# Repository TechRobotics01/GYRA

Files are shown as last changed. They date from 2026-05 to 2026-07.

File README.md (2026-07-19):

# GYRA 
So "GYRA" is a 3-axis stabilization gimbal system i built for phones and lighteight cameras more specifically point and shoot cameras<br>
GYRA is fully custom built from the 3D Design to the motherboard PCB all made by ME <br>
The name "GYRA" i derived from gyroscope which is a part of the MPU6050 sensor used in this project and GYRA also sounds pretty cool too <br>

# PURPOSE
So why exatly does this project exist <br>
This project exists because of a few reasons
- cheaper solution to ronin gymbals 
- extremely good learning project 
- fully custom built so i can easily add my own features

# FEATURES
- based on ESP32 S3 WROOM-1
- Fully custom 3D designed parts
- MPU6050 and HMC5883L used for motion tracking
- Portable design
- Custom PCB
- Designed for phones / lightweight cameras (upto ~ 200g)

# HOW DOES IT WORK
The mpu6050 and HMC5883L countinuously track the relative motion of the gimbal and then send the signals to the motherboard the ESP32 based motherboard then processes the signals to understand the orientation and run 3 seperate PID loops for 3 seperate axes namely 
- YAW
- ROLL
- PITCH
After the signals are passed through an Alpha filter for clearning the NOISE then are send to their respective PID loop the values i found which work for this system are
- For roll and Pitch axis
- Kp->1.2
- Ki->0
- Kd->0.1

I havent't really found the perfect values for the yaw axis as the yaw axis is the most unstable axis of the 3 axes and needs propery callibration  even more precise PID tuning for proper axis stability 

These 3 PID loops are the heart of the program these loops need to be very precise for proper theoretical working of the system <br>
I have a very good reason why i am using the word Theoretical
because in reality the project suffered from bracket instability joint wobble and print arm fles during the prototype phase which i worked hard to eliminate in MARK-1

# HARDWARE
## 3D PRINTABLE ASSEMBLY 
here is a render of the 3D printable design 
GYRA marl-1 with camera
GYRA EXPLODED PNG
The entire assembly consists of a total of 6 files which are 
- HEXALEGGED BASE (PCB housing)
- PCB HOUSING LID
- BASE HANDEL
- YAW ARM
- YAW--ROLL ARM
- ROLL--PITCH ARM
All of these are connected by mostly standard M3 screws whereas M2 screws may be required at some places such as the last 2 screws at ever arm of the 25T Aluminium CNC servo spline

## PCB / elecronics 
The pcb consists of the following majour parts 
- ESP32 S3 WROOM-1 module
- JST Connectors for
  - MPU6050 (4-pinJST)
  - HMC5883L (4-pinJST)
  - SERVOS(incuding GND) (4-pinJST)
  - Battery connector (2Pin JST)
- Decoupling capacitors
- IO0 and EN switched (SMD)
- M3 mounting hole




Now here comes the important part for the connnections so no-1 you need to first of all connect the 6-li-ion battries enclosed in the base handle to a 2S BMS module and to a DC femlae jack for charging and then you need to diectly connect the VCCs and GNDs of the servos to the BMS module and now you need to make a 4 pin JST connector which is basically 3 pins for servos yaw-roll-pitch respectively and final pin GND.

Now after this you need to  take the battry 7.4V and then connect it directly to the PCB as the PCB has a internal Step-Down voltage circuit but you need to be careful with the polarity. 

Please refer to the PCB schematics while hotplate soldering / assembling your PCB because the BARE PCB does not have much marking as to such where which pin should be conected 

# ZINE PAGE 
GYRA

# BUILT IRL 
Demo Video- https://youtu.be/y3TJgLPC-Hc





GYRA has been built IRL!

# HOW TO BUILD IT FOR YOURSELF 
So you want to make this project for yourself too <br>
I have included each and every file and component that you will require in this repository and BOM 
STEP-1
- Buy all the parts in the BOM
- Print the parts inside the Mark-1--->>STEP FILE folder (total of 6 parts)
- Get the PCB fabricated and solder all the components neatly using the HOTPLATE
- Test the PCB for any imporperly soldered parts/components
- Assemble the pcb inside the 3D printed hexalegged base using M2 screws
- Now connect the battries in a 2S3P manner
- Cut and strip the wires and make it into a JST connector
  - 1 FOR MPU6050
  - 1 FOR HMC5883L
  - 1 FOR SERVOS AND GND PIN
  - 1 FOR THE BATTERY connector
  - Solder the battery connections as stated under the "PCB / electronics part" and then house the battires inside the base handle
  - Join the hexalegged base to the pcb lid using M3 and M2 screws whereever needed
  - now assemble the above appembly consisting of
    - Servos
    - IMUs
    - YAW arm
    - YAW---PITCH arm
    - PITCH----ROLL arm
    - And then finally connect the 1/4th inch thread to the print
    - Connect your camera or phone adapter
    - Finally please use the code to TUNE your gimbal different tuning values are needed for different cameras because center of mass and orientation
    - Affect the PID constants a lot
    - After tuning your gimbal please hardcode the values into the gimbal (more info on that in a few days)
    - And finally enjoy a gimbal you made!!!!  
    WARNING: you may need to heat the 1/4th inch screw to 100*C so it can be properly housed inside the PITCH arm

# PROBLEMS FACED
there were a lot of problems i faced during the development of this project i have all the prototypes saved in subfolders in the CAD filder this project had a total of 5 iterated prototypes before i made the actual MARK-1 <br>
so here is a list of probelms i faced <br>

So first of all i had no inspiration and was designing the structure i had in my head when i built and tested the first printed prototype i found out many many fatal flaws such as the biggest one being that the roll arm was colliding with the base of the YAW arm where the sensor was seated and also that the motor constrians were misjudged second of all the arms were flexing because i made then longer than they needed to be and the arm used to jitter and shake because the motor could not take the load of the heavy arms and assembly <br>

after like 3 iterations i finally took a bit of inspiration from ronin's gimbal and finally understood how the gimabl's standard structure should actually be first of all i was veru skeptical about if the motors could move the long arms or not as the length of the arms were almost excedding  the torue the motors could produced but once it was assembeled nd i tested it....IT worked just fine <br>

Now here comes the biggest challenge i faced almost throughtout the project so first of alli was using MG995 motors's plastic head and attachments to connect the 3D printed arm with the motor which was an bad idea because it already had a bit of play which was only made worse by the motor repeatedly moving and wearking out the joint's teeth during Prottype's PID tuning and i found out the solution to this when i was sitting in my room at 12 AM and the idea of using CNC Aluminium 25T servo spline arm <br>

 This thing and now i designed the nre joint in accordance to the dimension's of the spline and i used properl M3 and M2 screws to mount the print on this isntead of using improper sized M2.2 screws everywhere and hoping it would work 

 Overall this project was one of the best learning project i had made because it taught me many things related to 3D printing CAD and print tolerances
 and also sharpened my skills of PCB and Embedded design design and overall project design and workflow 
 The multiple failed prototypes challenged the appumptions i made and i developed a new kind of more efficient workflow than before 
 
### I SPENT A TOTAL OF ~68 HOURS ON THIS PROJECT ###

# CREDITS 
- ME
- google.com
- chatgpt (FOR DEBUGGING AND GUIDANCE ONLY)
- [randomnerdtutorial.com](https://randomnerdtutorials.com/)

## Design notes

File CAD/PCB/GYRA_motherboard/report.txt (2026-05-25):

Plotted to 'C:\Users\DELL\Desktop\MISSION FALLOUT\GYRA\GYRA\CAD\PCB\GYRA_motherboard\GYRA_motherboard-F_Cu.gbr'.
Plotted to 'C:\Users\DELL\Desktop\MISSION FALLOUT\GYRA\GYRA\CAD\PCB\GYRA_motherboard\GYRA_motherboard-B_Cu.gbr'.
Plotted to 'C:\Users\DELL\Desktop\MISSION FALLOUT\GYRA\GYRA\CAD\PCB\GYRA_motherboard\GYRA_motherboard-F_Paste.gbr'.
Plotted to 'C:\Users\DELL\Desktop\MISSION FALLOUT\GYRA\GYRA\CAD\PCB\GYRA_motherboard\GYRA_motherboard-B_Paste.gbr'.
Plotted to 'C:\Users\DELL\Desktop\MISSION FALLOUT\GYRA\GYRA\CAD\PCB\GYRA_motherboard\GYRA_motherboard-F_Silkscreen.gbr'.
Plotted to 'C:\Users\DELL\Desktop\MISSION FALLOUT\GYRA\GYRA\CAD\PCB\GYRA_motherboard\GYRA_motherboard-B_Silkscreen.gbr'.
Plotted to 'C:\Users\DELL\Desktop\MISSION FALLOUT\GYRA\GYRA\CAD\PCB\GYRA_motherboard\GYRA_motherboard-F_Mask.gbr'.
Plotted to 'C:\Users\DELL\Desktop\MISSION FALLOUT\GYRA\GYRA\CAD\PCB\GYRA_motherboard\GYRA_motherboard-B_Mask.gbr'.
Plotted to 'C:\Users\DELL\Desktop\MISSION FALLOUT\GYRA\GYRA\CAD\PCB\GYRA_motherboard\GYRA_motherboard-Edge_Cuts.gbr'.
Created Gerber job file 'C:\Users\DELL\Desktop\MISSION FALLOUT\GYRA\GYRA\CAD\PCB\GYRA_motherboard\GYRA_motherboard-job.gbrjob'.
Info: Done.
Info: Done.

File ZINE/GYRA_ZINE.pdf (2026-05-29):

# GYRA

## A Fully Custom Built 3-Axis Gimbal

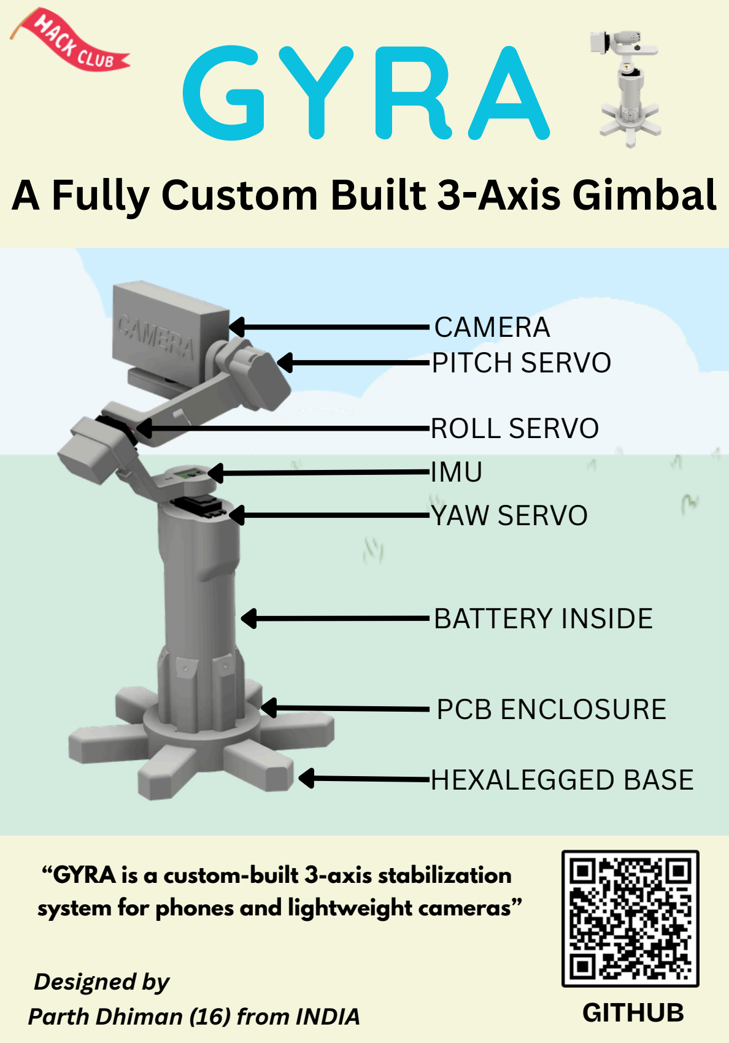
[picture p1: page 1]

HEXALEGGED BASE

BATTERY INSIDE

PCB ENCLOSURE

IMU

PITCH SERVO

“GYRA is a custom-built 3-axis stabilization system for phones and lightweight cameras”

YAW SERVO

ROLL SERVO

Parth Dhiman (16) from INDIA

GITHUB

CAMERA

Designed by

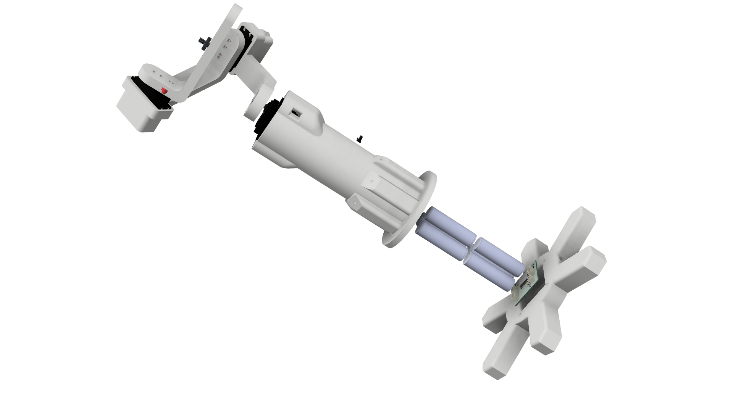
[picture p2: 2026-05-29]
RENDERS/MARK-1 RENDERS/GYRA EXPLODED PNG.png

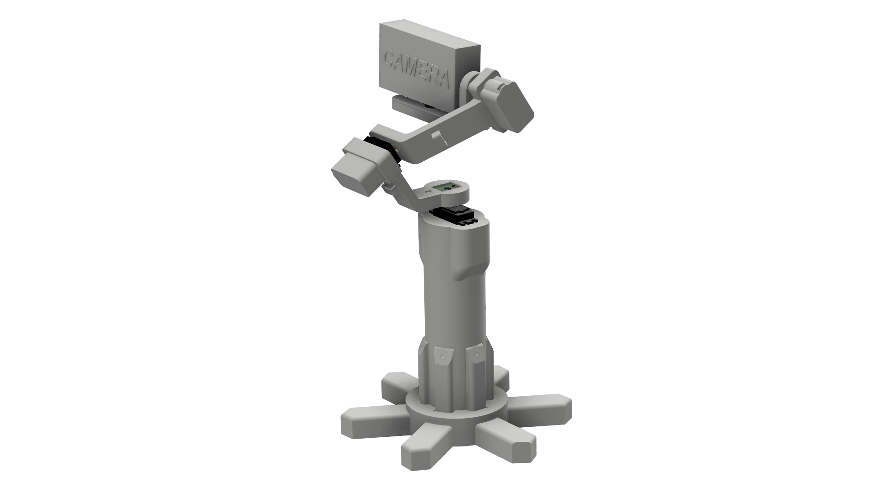
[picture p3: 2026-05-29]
RENDERS/MARK-1 RENDERS/GYRA marl-1 with camera.png

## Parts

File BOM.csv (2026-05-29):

S. No | Part Name | Qty required | Qty Purchased | Cost per Unit($) | Shipping cost ($) | Total cost ($) | Status | Supplier | Purchase Link
1 | 1kg PLA+(eSun) | 1 | 1 | 11.49 | NA | 11.49 | Needed | robocraze | https://robocraze.com/products/esun-pla-basic-1-75mm-1kg-3d-printing-filament-black-color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
2 | MPU6050 | 1 | 1 | NA | NA | NA | Already owned | NA | NA
3 | HMC5883L | 1 | 1 | 1.98 | NA | 1.98 | Needed | robocraze | https://robocraze.com/products/hmc5883l-triple-axis-compass?variant=40192560857241
4 | MG995 servos | 3 | NA | NA | NA | NA | Already owned | NA | NA
5 | 18650 Li-ion battries | 6 | 6 | 0.72 | NA | 4.32 | Needed | robocraze | https://robocraze.com/products/3-7v-2000mah-18650-li-ion-battery?_pos=1&_sid=db8a20379&_ss=r
6 | 2S Li-Ion BMS | 1 | 1 | 0.37 | NA | 0.37 | Needed | makerbaxxar | https://makerbazar.in/products/18650-bms-lithium-battery-protection-board?variant=48251032731888
7 | DC power jack(male) | 1 | 1 | 0.089 | NA | 0.089 | Needed | makerbazzar | https://makerbazar.in/products/5-5-2-1mm-dc-power-jack-wire-with-open-end?variant=47599032140016
8 | DC power jack(female) | 1 | 1 | 0.094 | NA | 0.094 | Needed | maker bazzar | https://makerbazar.in/products/5-5-2-1mm-dc-power-jack-wire-with-open-end?variant=47599032172784
9 | PCB Fab. | 1 | 5 | 8.36 | 1.51 | 9.87 | Needed | LionCircuits | https://order.lioncircuits.com/cart
10 | M3 screws | 15 | NA | NA | NA | NA | Already owned | NA | NA
11 | M2 screws | 10 | 25 | 0.082 | 1.46 | 3.51 | Needed | Onlyscrews | https://onlyscrews.in/products/m2-x-10mm-hex-allen-socket-head-high-tensile12-9-black-oxide-screw-dia-2mm-length-10mm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
12 | 4pinJST Connector (female) | 4 | 4 | 0.17 | NA | 0.68 | Needed | Robu | https://robu.in/product/1-0c-04y-1mm-4-pin-ultra-thin-female-housing-connector-with-300mm-wire28-awg/
13 | 4pinJSt connector(male) | 4 | 4 | 0.048 | NA | 0.192 | Needed | Robu | https://robu.in/product/a2512wv-4p-cjt-4-pin-2-50mm-180-wafer-male-connector-rohs/
14 | 4.7uH inductor | 1 | 5 | 0.25 | NA | 1.25 | Needed | Robu | https://robu.in/product/cd43-4-7%C2%B5h-1a-smd-power-inductor-5-pcs/
15 | DIODES AP63203WU-7 | 1 | 2 | 0.9 | 1.05 | 2.86 | Needed | LionCircuits | https://www.lioncircuits.com/parts/AP63203WU-7
16 | ESP32 S3 WROOM-1 | 1 | 1 | 4.5 | 0.89 | 5.39 | Needed | Techeism | https://techiesms.com/product/esp32-s3-wroom-n16r8/
17 | Servo spline arm 25T | 3 | 3 | 0.68 | NA | 2.04 | Needed | Robu | https://robu.in/product/cnc-aluminum-steering-servo-horn-arm-futaba-standard-25t-aluminum/
18 | soldering station | 1 | 1 | 15 | NA | 15 | Needed | Robu | https://robu.in/product/yihua-926-upgrade-version-soldering-iron-station/
 |  |  |  |  | TOTAL COST | 59.135

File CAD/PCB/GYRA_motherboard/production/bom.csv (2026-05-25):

Designator | Footprint | Quantity | Value | LCSC Part #
C1 | 0805 | 1 | 1uF
C2, C8 | 0805 | 2 | 10uF
C3, C6 | 0805 | 2 | 0.1uF
C4, C5 | 0805 | 2 | 22uF
C7 | 0805 | 1 | 100nF
J1 | JST_XH_B4B-XH-A_1x04_P2.50mm_Vertical | 1 | MPU6050
J2 | JST_XH_B4B-XH-A_1x04_P2.50mm_Vertical | 1 | HMC5883L
J3 | JST_XH_B4B-XH-A_1x04_P2.50mm_Vertical | 1 | SERVOS
J4 | JST_XH_B2B-XH-A_1x02_P2.50mm_Vertical | 1 | 2S3P BAT
L1 | L_7.3x7.3_H4.5 | 1 | 3.9uH
R1, R2 | 0805 | 2 | 10KR
SW1 | SW_Push_1P1T_NO_CK_KMR2 | 1 | SW_EN
SW2 | SW_Push_1P1T_NO_CK_KMR2 | 1 | SW_IO0
U1 | ESP32-S3-WROOM-1 | 1 | ESP32-S3-WROOM-1
U2 | TSOT-23-6 | 1 | AP63203

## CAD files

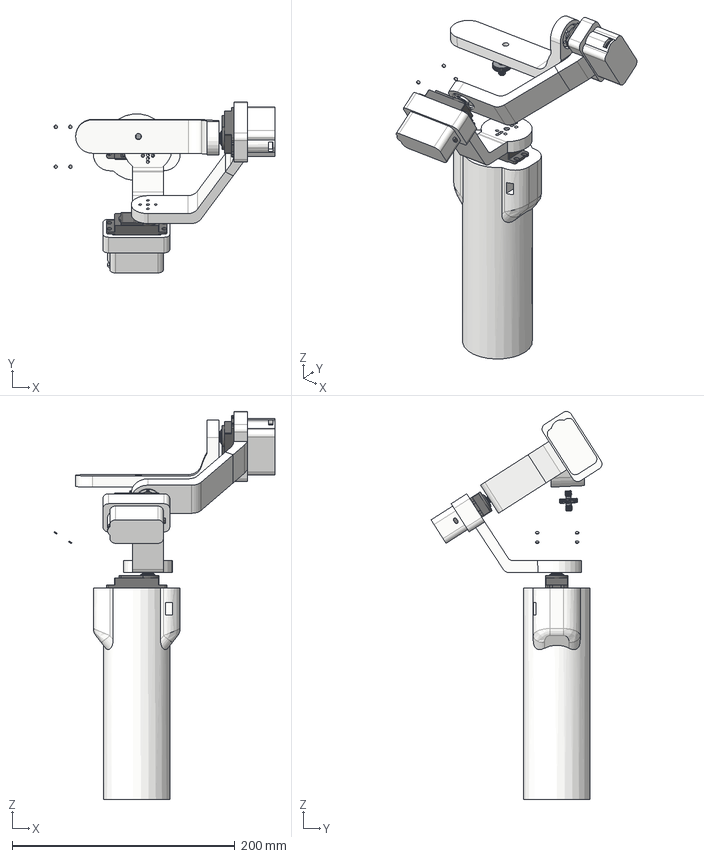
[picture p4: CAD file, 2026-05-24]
CAD/CAD 3D/MARK-1/ASSMEBLY STEP FILE/GYRA MARK-1 ASSEMBLY .step
198.2 x 153.4 x 348.3 mm
MG995_Gear2
Servo horn v2 x 2
GYRA ROLL PITCH BRAKET PROTOTYPE V2
GYRA PITCH BRACKET
ADAPTER_1-4_M_1-4_M.PRT
GYRA PITCH ARM V4
18650 Battery x 6
GYRO base handle axis 1 (yaw)

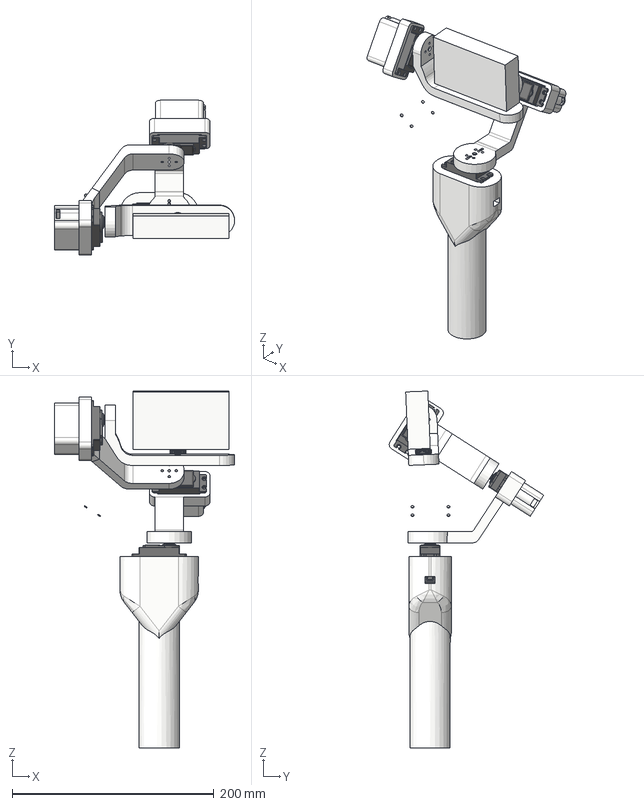
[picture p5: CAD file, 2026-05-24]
CAD/CAD 3D/PROTOTYPES/PROTOTYPE V5/ASSEMBLY/GYRA PROTOTYPE V5 FULL ASSEMBLY v13.step
178.9 x 153.4 x 354.3 mm
GYRO base handle axis 1 (yaw)
MG995_Gear2
Servo horn v2 x 2
GYRA ROLL PITCH BRAKET PROTOTYPE V2
GYRA PITCH BRACKET
ADAPTER_1-4_M_1-4_M.PRT
GYRA PITCH ARM V4

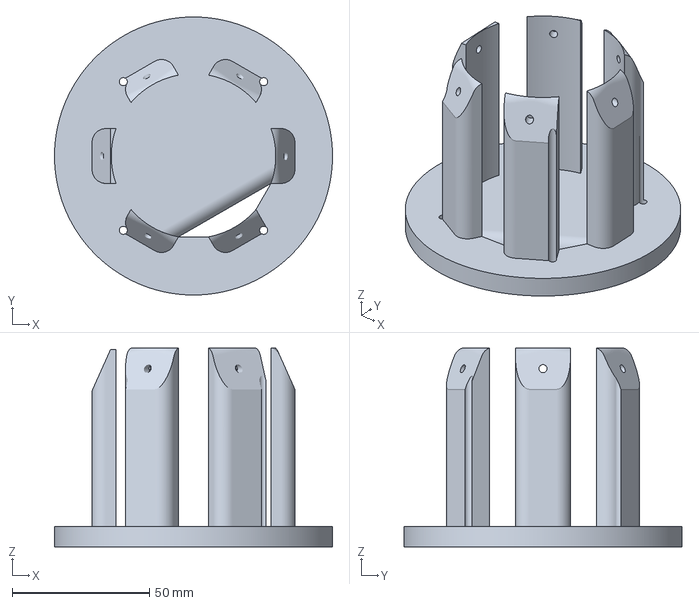
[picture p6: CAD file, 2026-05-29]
CAD/CAD 3D/MARK-1/3D PRINT FILES/BAMBU SLICER/GYRA PCB BASE LID v8.3mf
101.4 x 101.4 x 72.5 mm

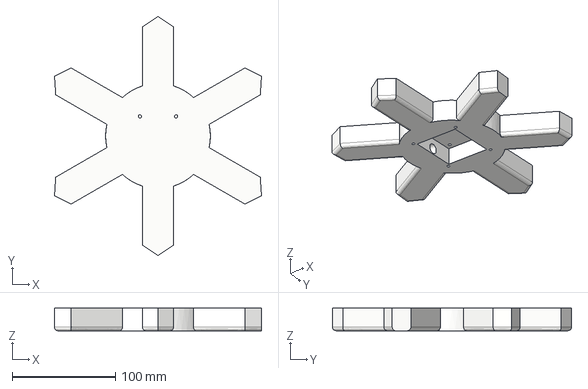
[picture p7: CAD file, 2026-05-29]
CAD/CAD 3D/MARK-1/3D PRINT FILES/STEP FILES/GYRA BASE PCB ENCLOSURE v9.step
200.4 x 231.4 x 22.0 mm

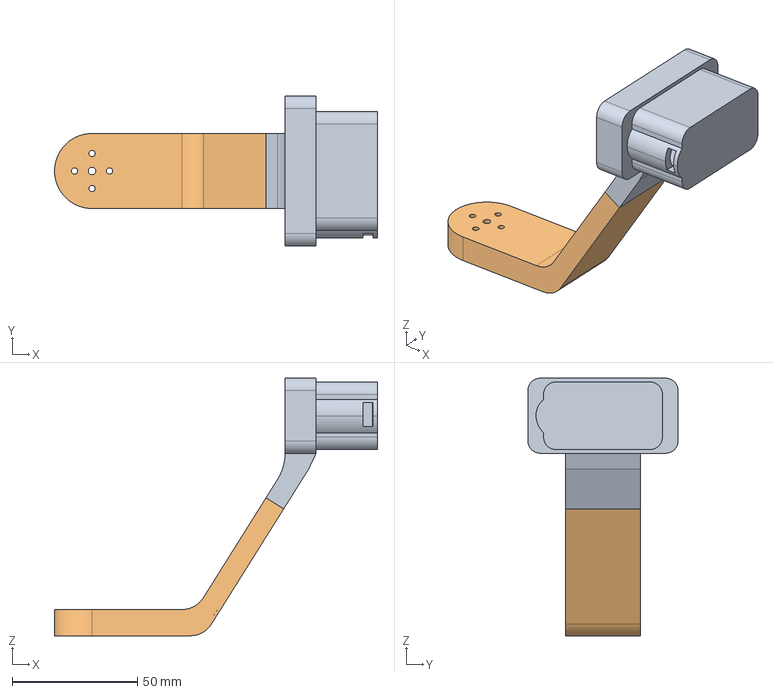
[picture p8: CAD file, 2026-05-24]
CAD/CAD 3D/PROTOTYPES/PROTOTYPE V5/3D PRINTABLES/GYRA PITCH BRACKET v31(PRT 2).step
129.0 x 60.0 x 102.9 mm

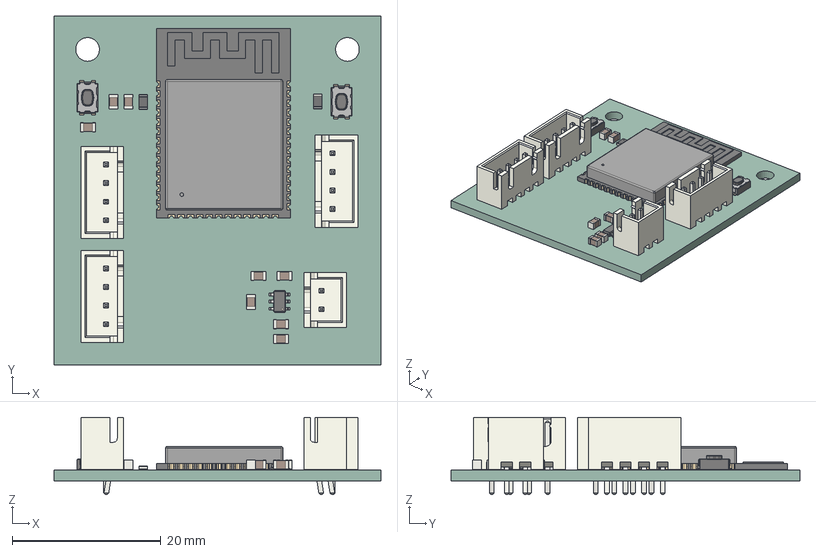
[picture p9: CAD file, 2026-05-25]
CAD/PCB/PCB_STEP_FILE/GYRA_motherboard.step
44.0 x 47.0 x 10.4 mm
SW_Push_1P1T_NO_CK_KMR2 x 2
TSOT-23-6
JST_XH_B4B-XH-A_1x04_P2.50mm_Vertical x 3
C_0805_2012Metric x 8
ESP32-S3-WROOM-1
JST_XH_B2B-XH-A_1x02_P2.50mm_Vertical
R_0805_2012Metric x 2
GYRA_motherboard_PCB

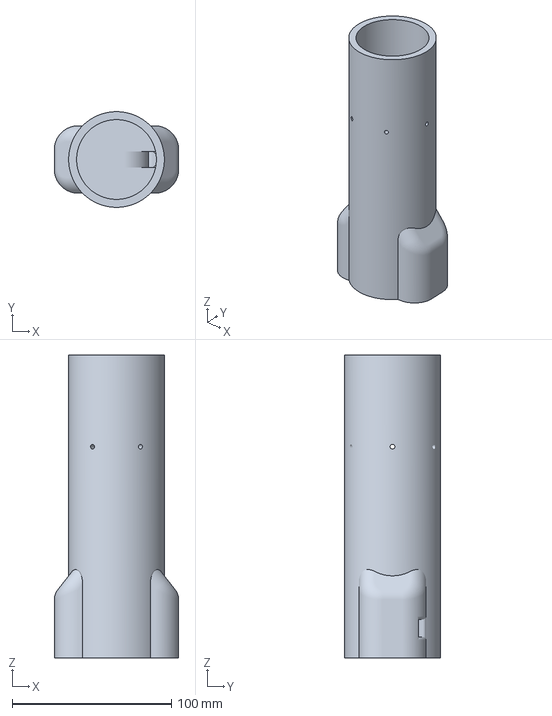
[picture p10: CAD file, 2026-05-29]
CAD/CAD 3D/MARK-1/3D PRINT FILES/BAMBU SLICER/GYRO base handle axis 1 (yaw) v12.3mf
78.0 x 60.0 x 190.0 mm

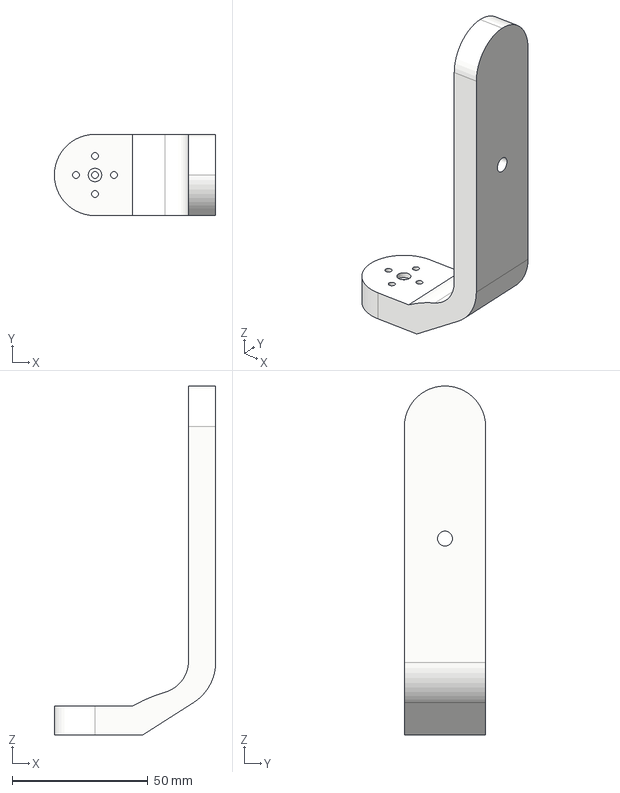
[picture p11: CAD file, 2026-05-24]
CAD/CAD 3D/PROTOTYPES/PROTOTYPE V5/3D PRINTABLES/GYRA PITCH ARM(PRT 1).step
59.5 x 30.0 x 128.8 mm

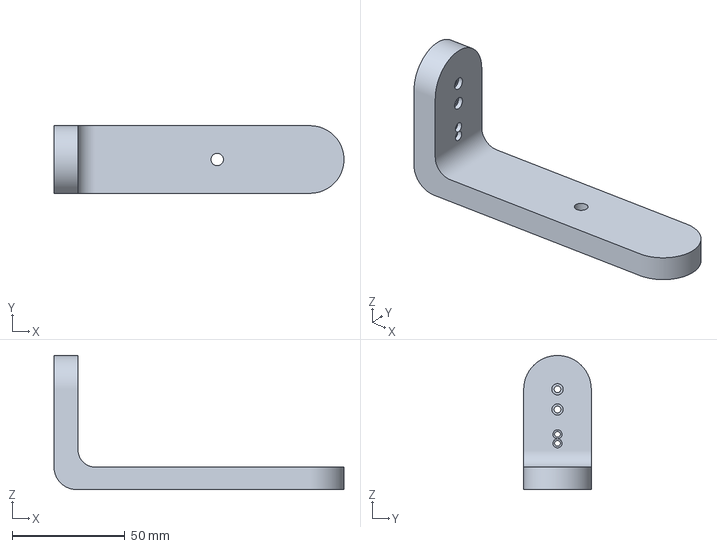
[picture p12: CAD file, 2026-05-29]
CAD/CAD 3D/MARK-1/3D PRINT FILES/BAMBU SLICER/GYRA PITCH ARM V4 v6.3mf
128.8 x 30.0 x 59.5 mm

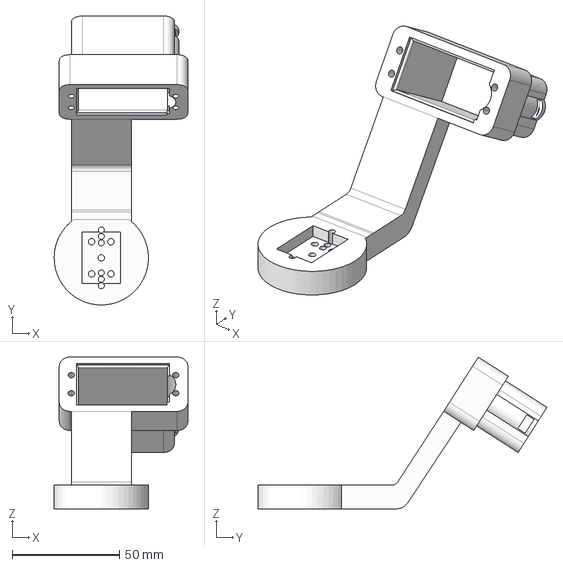
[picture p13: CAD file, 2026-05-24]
CAD/CAD 3D/PROTOTYPES/PROTOTYPE V5/3D PRINTABLES/GYRA ROLL PITCH BRAKET (PRT 3).step
62.4 x 134.8 x 70.8 mm

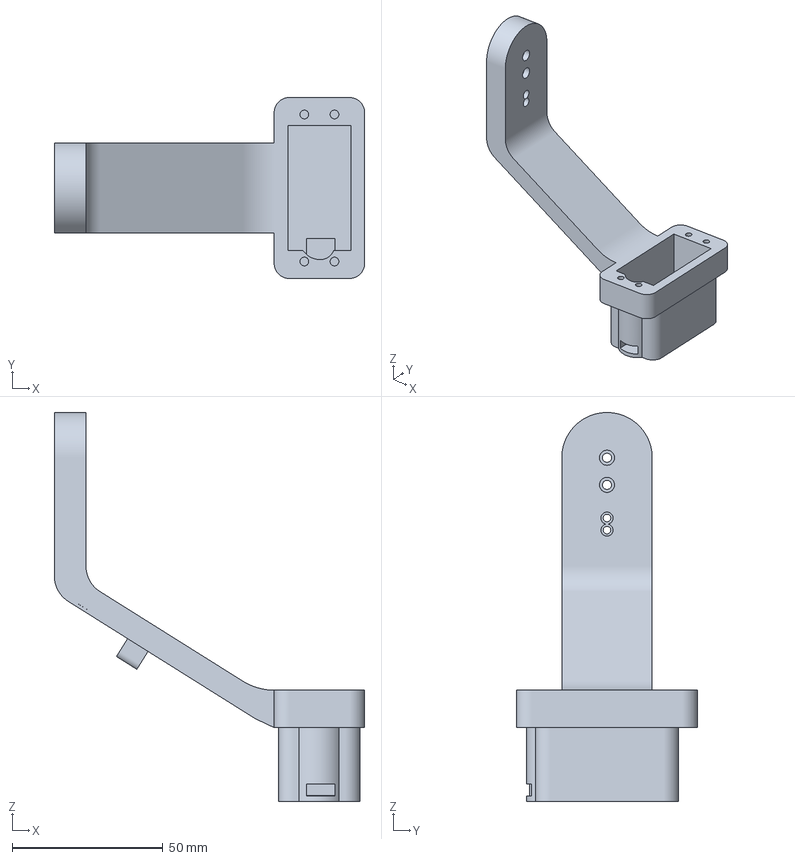
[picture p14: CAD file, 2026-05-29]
CAD/CAD 3D/MARK-1/3D PRINT FILES/BAMBU SLICER/GYRA PITCH BRACKET v4.3mf
102.9 x 60.0 x 129.0 mm

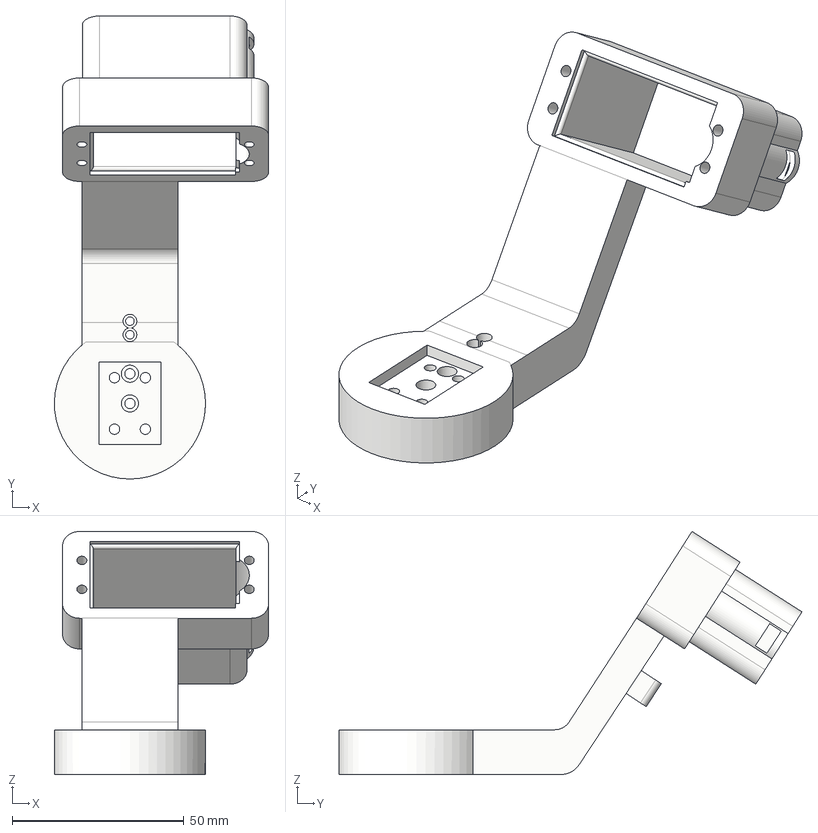
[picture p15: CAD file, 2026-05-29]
CAD/CAD 3D/MARK-1/3D PRINT FILES/STEP FILES/GYRA ROLL PITCH BRAKET PROTOTYPE V2 v7.step
62.4 x 134.8 x 70.8 mm

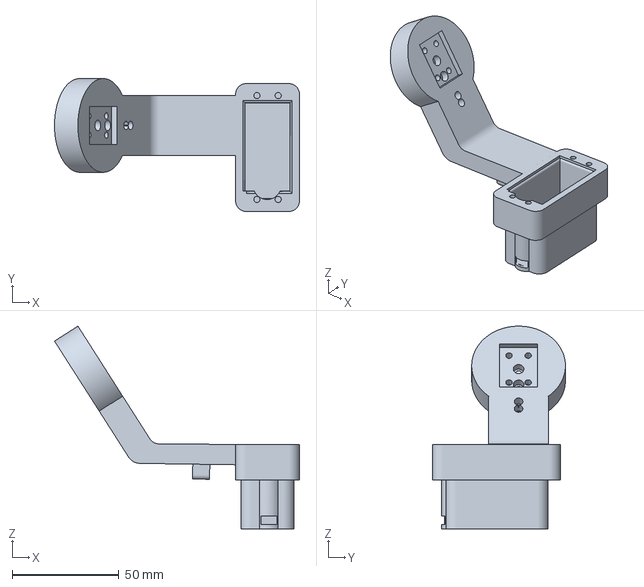
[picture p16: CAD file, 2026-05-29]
CAD/CAD 3D/MARK-1/3D PRINT FILES/BAMBU SLICER/GYRA ROLL PITCH BRAKET PROTOTYPE V2 v7.3mf
115.0 x 62.4 x 95.1 mm

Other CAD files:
CAD/CAD 3D/MARK-1/3D PRINT FILES/STEP FILES/GYRO base handle axis 1 (yaw) v12.step
CAD/CAD 3D/MARK-1/3D PRINT FILES/STEP FILES/GYRA PITCH ARM V4 v6.step
CAD/CAD 3D/MARK-1/3D PRINT FILES/STEP FILES/GYRA PITCH BRACKET v4.step
CAD/CAD 3D/MARK-1/3D PRINT FILES/BAMBU SLICER/GYRA BASE PCB ENCLOSURE v9.3mf
CAD/CAD 3D/MARK-1/3D PRINT FILES/STEP FILES/GYRA PCB BASE LID v8.step
CAD/CAD 3D/MARK-1/3D PRINT FILES/F3D FILES/GYRA BASE PCB ENCLOSURE v9.f3d
CAD/CAD 3D/MARK-1/3D PRINT FILES/F3D FILES/GYRA PCB BASE LID v8.f3d
CAD/CAD 3D/MARK-1/3D PRINT FILES/F3D FILES/GYRA PITCH ARM V4 v6.f3d
CAD/CAD 3D/MARK-1/3D PRINT FILES/F3D FILES/GYRA PITCH BRACKET v4.f3d
CAD/CAD 3D/MARK-1/3D PRINT FILES/F3D FILES/GYRA ROLL PITCH BRAKET PROTOTYPE V2 v7.f3d
CAD/CAD 3D/MARK-1/3D PRINT FILES/F3D FILES/GYRO base handle axis 1 (yaw) v12.f3d
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

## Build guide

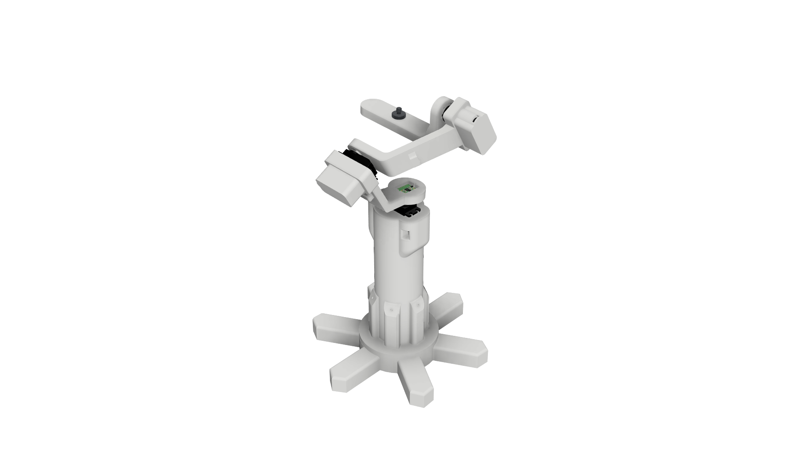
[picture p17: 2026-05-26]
RENDERS/MARK-1 RENDERS/GYRA PROTOTYPE MARK-1 FULL ASSEMBLY R2.png

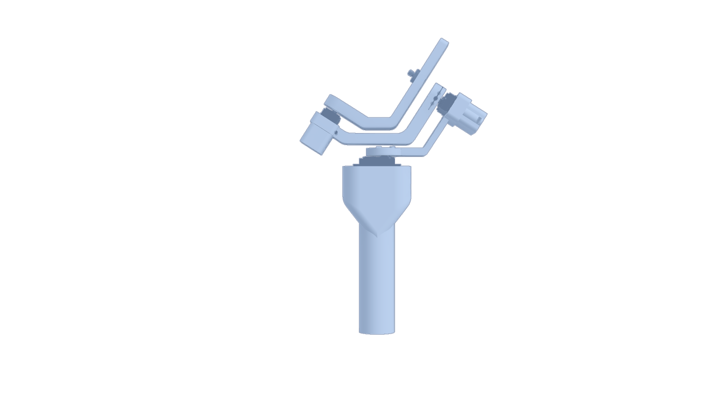
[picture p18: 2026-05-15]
RENDERS/PROTOTYPE RENDERS/GYRA PROTOTYPE V2 FULL ASSEMBLY v6.png

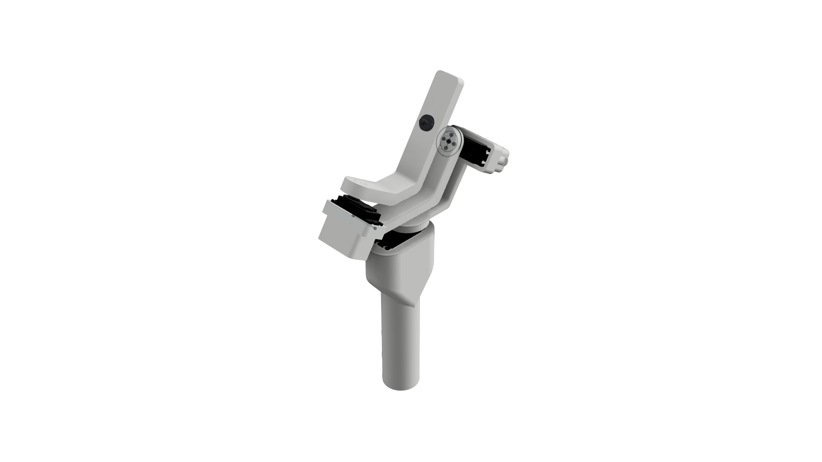
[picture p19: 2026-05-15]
RENDERS/PROTOTYPE RENDERS/GYRA PROTOTYPE V2 FULL ASSEMBLY v6 pic2.png

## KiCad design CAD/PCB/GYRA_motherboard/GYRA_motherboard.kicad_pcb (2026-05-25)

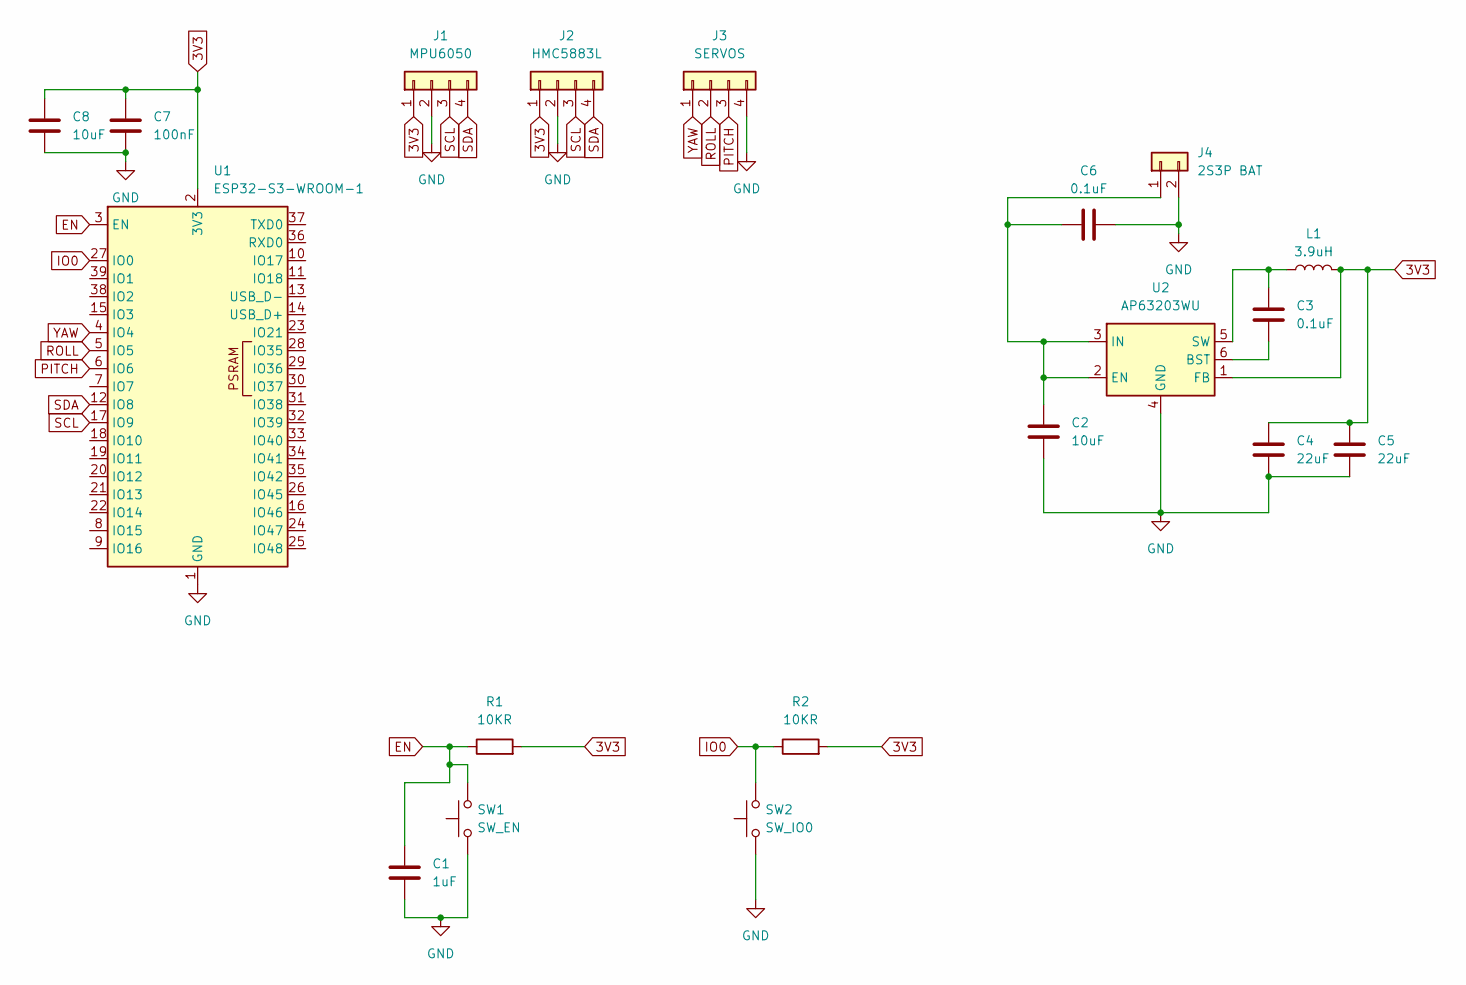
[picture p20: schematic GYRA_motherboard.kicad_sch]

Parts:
C1: 1uF; C_0805_2012Metric
C2, C8: 10uF; C_0805_2012Metric
C3, C6: 0.1uF; C_0805_2012Metric
C4, C5: 22uF; C_0805_2012Metric
C7: 100nF; C_0805_2012Metric
J1: MPU6050; JST_XH_B4B-XH-A_1x04_P2.50mm_Vertical
J2: HMC5883L; JST_XH_B4B-XH-A_1x04_P2.50mm_Vertical
J3: SERVOS; JST_XH_B4B-XH-A_1x04_P2.50mm_Vertical
J4: 2S3P BAT; JST_XH_B2B-XH-A_1x02_P2.50mm_Vertical
L1: 3.9uH; L_7.3x7.3_H4.5
R1, R2: 10KR; R_0805_2012Metric
SW1: SW_EN; SW_Push_1P1T_NO_CK_KMR2
SW2: SW_IO0; SW_Push_1P1T_NO_CK_KMR2
U1: ESP32-S3-WROOM-1
U2: AP63203WU; TSOT-23-6

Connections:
3V3: C4.1, C5.1, C7.1, C8.1, J1.1, J2.1, L1.2, R1.2, R2.2, U1.2 (3V3), U2.1 (FB)
EN: C1.2, R1.1, SW1.2, U1.3 (EN)
GND: C1.1, C2.2, C4.2, C5.2, C6.2, C7.2, C8.2, J1.2, J2.2, J3.4, J4.2, SW1.1, SW2.1, U1.1 (GND), U1.40 (GND), U1.41 (GND), U2.4 (GND)
IO0: R2.1, SW2.2, U1.27 (IO0)
unnamed: C2.1, C6.1, J4.1, U2.2 (EN), U2.3 (IN)
unnamed: C3.2, U2.6 (BST)
unnamed: C3.1, L1.1, U2.5 (SW)
PITCH: J3.3, U1.6 (IO6)
ROLL: J3.2, U1.5 (IO5)
SCL: J1.3, J2.3, U1.17 (IO9)
SDA: J1.4, J2.4, U1.12 (IO8)
YAW: J3.1, U1.4 (IO4)

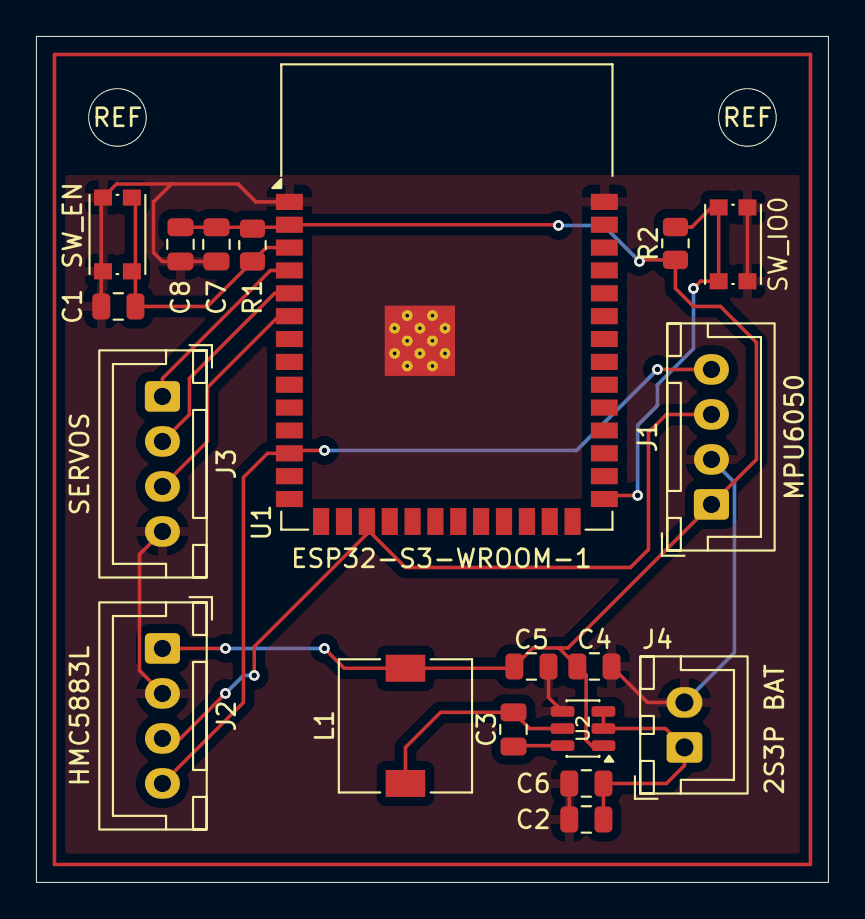
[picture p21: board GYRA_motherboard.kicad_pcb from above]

Board: 2 copper layers, 44.0 x 47.0 mm, 21 parts (0 on the bottom side), 12 nets.

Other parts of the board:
REF: M3; MountingHole_3.2mm_M3
REF#2: M3; MountingHole_3.2mm_M3

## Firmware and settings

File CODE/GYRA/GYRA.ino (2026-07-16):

#include <Wire.h>
#include <Adafruit_MPU6050.h>
#include <Adafruit_Sensor.h>
#include <PID_v1.h>
#include <esp_task_wdt.h>
#include <esp_system.h>
#include <cstdarg>
#include <math.h>

Adafruit_MPU6050 mpu; 

// ---------- PINS ----------
const int SDA_PIN    = 8;
const int SCL_PIN    = 9;

const int SERVO_PINR = 5; // Roll Servo Pin
const int SERVO_PINP = 6; // Pitch Servo Pin

// ---------- PID ROLL ----------
double input = 0, output = 0, setpoint = 0;
double Kp = 1.2;  // Activated and matched to Pitch for instant testing
double Ki = 0.0;
double Kd = 0.1;
PID myPID(&input, &output, &setpoint, Kp, Ki, Kd, DIRECT);

// ---------- PID PITCH ----------
double inputP = 0, outputP = 0, setpointP = 0;
double KpP = 1.2;
double KiP = 0.0;
double KdP = 0.1;
PID pidPitch(&inputP, &outputP, &setpointP, KpP, KiP, KdP, DIRECT);

// ---------- FILTER ----------
float angle = 0.0;
float pitch = 0.0;
float gyroBiasY = 0.0;
float gyroBiasX = 0.0;
unsigned long lastTime = 0;

// ---------- SERVO SMOOTHING ----------
float servoSmooth = 90.0;
float servoPitch  = 90.0;

// ---------- WATCHDOG ----------
#define WDT_TIMEOUT_SEC 5

// ═══════════════════════════════════════
// DEBUG & LOGGING SYSTEM
// ═══════════════════════════════════════
enum DebugLevel {
    LEVEL_NONE,
    LEVEL_ERROR,
    LEVEL_WARNING,
    LEVEL_INFO,
    LEVEL_VERBOSE
};

DebugLevel currentLogLevel = LEVEL_VERBOSE; 

#define ANSI_RESET   "\033[0m"
#define ANSI_RED     "\033[31m"
#define ANSI_YELLOW  "\033[33m"
#define ANSI_GREEN   "\033[32m"
#define ANSI_CYAN    "\033[36m"

void debugPrint(DebugLevel level, const char *format, ...) {
    if (level > currentLogLevel) return;
    
    switch (level) {
        case LEVEL_ERROR:   Serial.print(ANSI_RED "[ERROR] " ANSI_RESET); break;
        case LEVEL_WARNING: Serial.print(ANSI_YELLOW "[WARNING] " ANSI_RESET); break;
        case LEVEL_INFO:    Serial.print(ANSI_GREEN "[INFO] " ANSI_RESET); break;
        case LEVEL_VERBOSE: Serial.print(ANSI_CYAN "[VERBOSE] " ANSI_RESET); break;
        default: break;
    }
    
    char buffer[256];
    va_list args;
    va_start(args, format);
    vsnprintf(buffer, sizeof(buffer), format, args);
    va_end(args);
    
    Serial.println(buffer);
}

#define DEBUG_ERROR(fmt, ...)   debugPrint(LEVEL_ERROR, fmt, ##__VA_ARGS__)
#define DEBUG_WARNING(fmt, ...) debugPrint(LEVEL_WARNING, fmt, ##__VA_ARGS__)
#define DEBUG_INFO(fmt, ...)    debugPrint(LEVEL_INFO, fmt, ##__VA_ARGS__)
#define DEBUG_VERBOSE(fmt, ...) debugPrint(LEVEL_VERBOSE, fmt, ##__VA_ARGS__)

// ═══════════════════════════════════════
// NATIVE SERVO DRIVER
// ═══════════════════════════════════════
void setServoAngle(int pin, int angle) {
  // Maps 0-180 degrees to standard 500us - 2400us pulses using 12-bit PWM (0-4095) at 50Hz
  int duty = map(constrain(angle, 0, 180), 0, 180, 102, 491);
  analogWrite(pin, duty);
}

// ═══════════════════════════════════════
// TIMING & DIAGNOSTICS GLOBALS
// ═══════════════════════════════════════
unsigned long loopTimeMin = 999999;
unsigned long loopTimeMax = 0;
unsigned long loopTimeSum = 0;
unsigned long loopCount   = 0;

unsigned long lastLoopStatsTimer = 0;
unsigned long lastMemTimer       = 0;
unsigned long lastHealthTimer    = 0;
unsigned long lastTelemetryTimer = 0;
unsigned long lastSatWarning     = 0;

// ═══════════════════════════════════════
// CRASH DIAGNOSTICS
// ═══════════════════════════════════════
void printCrashDiagnostics() {
    esp_reset_reason_t reason = esp_reset_reason();
    if (reason != ESP_RST_POWERON && reason != ESP_RST_SW && reason != ESP_RST_EXT) {
        Serial.println(ANSI_RED "\n===========================");
        Serial.println("    SYSTEM FAULT DETECTED");
        Serial.println("===========================" ANSI_RESET);
        Serial.printf("Reason Code: %d\n", reason);
        Serial.printf("Free Heap: %u Bytes\n", ESP.getFreeHeap());
        Serial.println("Attempting Recovery...\n");
        delay(1000);
    }
}

// ═══════════════════════════════════════
// GYRO CALIBRATION
// ═══════════════════════════════════════
void calibrateGyro() {
  DEBUG_INFO("Keeping still for Gyroscope Calibration...");
  const int N = 300;
  float sumY = 0, sumX = 0;
  
  for (int i = 0; i < N; i++) {
    sensors_event_t a, g, t;
    mpu.getEvent(&a, &g, &t);
    sumY += g.gyro.y;
    sumX += g.gyro.x;
    esp_task_wdt_reset();
    delay(5);
  }
  gyroBiasY = sumY / N;
  gyroBiasX = sumX / N;
  Serial.println("GYRO CALIBRATION COMPLETE\n");
}

// ═══════════════════════════════════════
// I2C RECOVERY
// ═══════════════════════════════════════
void recoverI2CBus() {
  pinMode(SDA_PIN, INPUT_PULLUP);
  pinMode(SCL_PIN, OUTPUT);
  for (int i = 0; i < 9; i++) {
    digitalWrite(SCL_PIN, LOW);   delayMicroseconds(5);
    digitalWrite(SCL_PIN, HIGH);  delayMicroseconds(5);
  }
  pinMode(SDA_PIN, OUTPUT);
  digitalWrite(SDA_PIN, LOW);     delayMicroseconds(5);
  digitalWrite(SCL_PIN, HIGH);    delayMicroseconds(5);
  digitalWrite(SDA_PIN, HIGH);    delayMicroseconds(5);
}

// ═══════════════════════════════════════
// SETUP
// ═══════════════════════════════════════
void setup() {
  Serial.begin(115200);
  delay(2000);
  
  printCrashDiagnostics();

  Serial.println("\n===========================");
  Serial.println(" GYRA 2-AXIS STARTUP DIAG");
  Serial.println("===========================");
  
  Serial.printf("ESP32 Boot..............PASS\n");
  Serial.printf("Free Heap...............%u Bytes\n\n", ESP.getFreeHeap());

  // Configure Watchdog
  esp_task_wdt_config_t wdt_config = {
    .timeout_ms     = WDT_TIMEOUT_SEC * 1000,
    .idle_core_mask = (1 << portNUM_PROCESSORS) - 1,
    .trigger_panic  = true
  };
  esp_task_wdt_reconfigure(&wdt_config);
  esp_task_wdt_add(NULL);

  Serial.print("Running I2C Recovery....");
  recoverI2CBus();
  Serial.println("PASS");

  Serial.print("Initializing I2C........");
  Wire.begin(SDA_PIN, SCL_PIN);
  Wire.setClock(100000);
  Wire.setTimeOut(50);
  delay(100);
  Serial.println("PASS\n");

  Serial.print("Initializing MPU6050...");
  bool mpuReady = false;
  int retryCount = 0;
  while (!mpuReady && retryCount < 6) {
    if (mpu.begin(0x68, &Wire)) {
      mpuReady = true;
    } else {
      retryCount++;
      Serial.print(".");
      esp_task_wdt_reset();
      delay(500);
    }
  }

  if (!mpuReady) {
    Serial.println("FAILED");
    while (1) { esp_task_wdt_reset(); delay(1000); }
  }
  Serial.println("PASS");

  mpu.setAccelerometerRange(MPU6050_RANGE_4_G);
  mpu.setGyroRange(MPU6050_RANGE_500_DEG);
  mpu.setFilterBandwidth(MPU6050_BAND_21_HZ);
  
  myPID.SetTunings(Kp, Ki, Kd);
  pidPitch.SetTunings(KpP, KiP, KdP);

  calibrateGyro();

  // Configure Native PWM Servos for Roll and Pitch
  Serial.print("Configuring Native PWM Servos...");
  analogWriteResolution(SERVO_PINR, 12); analogWriteFrequency(SERVO_PINR, 50);
  analogWriteResolution(SERVO_PINP, 12); analogWriteFrequency(SERVO_PINP, 50);
  Serial.println("PASS");
  
  // Park servos at center
  setServoAngle(SERVO_PINR, 90); 
  setServoAngle(SERVO_PINP, 90); 
  delay(300);

  myPID.SetOutputLimits(-90, 90);
  pidPitch.SetOutputLimits(-90, 90);

  myPID.SetMode(AUTOMATIC);
  pidPitch.SetMode(AUTOMATIC);

  Serial.println("\n===========================");
  DEBUG_INFO("2-Axis System Ready.");
  Serial.println("===========================\n");
  
  lastTime = micros();
  unsigned long mNow = millis();
  lastLoopStatsTimer = mNow;
  lastMemTimer       = mNow;
  lastHealthTimer    = mNow;
  lastTelemetryTimer = mNow;
}

// ═══════════════════════════════════════
// NaN & Bounds Protection 
// ═══════════════════════════════════════
bool isDataValid(sensors_event_t& a, sensors_event_t& g) {
    if (isnan(a.acceleration.x) || isinf(a.acceleration.x)) return false;
    if (isnan(a.acceleration.y) || isinf(a.acceleration.y)) return false;
    if (isnan(a.acceleration.z) || isinf(a.acceleration.z)) return false;
    if (isnan(g.gyro.x) || isinf(g.gyro.x)) return false;
    if (isnan(g.gyro.y) || isinf(g.gyro.y)) return false;
    if (isnan(g.gyro.z) || isinf(g.gyro.z)) return false;
    if (fabs(a.acceleration.x) > 50.0 || fabs(a.acceleration.y) > 50.0 || fabs(a.acceleration.z) > 50.0) return false;
    if (fabs(g.gyro.x) > 12.0 || fabs(g.gyro.y) > 12.0 || fabs(g.gyro.z) > 12.0) return false;
    return true;
}

// ═══════════════════════════════════════
// MAIN LOOP
// ═══════════════════════════════════════
void loop() {
  unsigned long loopStartMicros = micros();
  unsigned long currentMillis   = millis();

  sensors_event_t a, g, t;
  mpu.getEvent(&a, &g, &t);
  
  if (!isDataValid(a, g)) {
      DEBUG_ERROR("Sensor Fault Detected / Skipping Data Frame");
      esp_task_wdt_reset();
      delay(10);
      return;
  }

  unsigned long now = micros();
  float dt = (now - lastTime) / 1000000.0f;
  lastTime = now;
  if (dt <= 0 || dt > 0.05f) dt = 0.01f;

  // ---------- ROLL CALCULATION ----------
  float accAngle = atan2f(-a.acceleration.x, sqrtf(a.acceleration.y * a.acceleration.y + a.acceleration.z * a.acceleration.z)) * RAD_TO_DEG;
  float gyroRate = (g.gyro.y - gyroBiasY) * RAD_TO_DEG;
  angle = 0.98f * (angle + gyroRate * dt) + 0.02f * accAngle;

  // ---------- PITCH CALCULATION ----------
  float accPitch = atan2f(a.acceleration.y, sqrtf(a.acceleration.x * a.acceleration.x + a.acceleration.z * a.acceleration.z)) * RAD_TO_DEG;
  float gyroPitch = (g.gyro.x - gyroBiasX) * RAD_TO_DEG;
  pitch = 0.98f * (pitch + gyroPitch * dt) + 0.02f * accPitch;

  // ---------- PID COMPUTE ----------
  input  = angle; myPID.Compute();
  inputP = pitch; pidPitch.Compute();

  // ---------- TARGET GENERATION ----------
  float targetRoll  = 92.0f + output;
  float targetPitch = 90.0f - outputP;

  // ---------- LOW-PASS SERVO SMOOTHING ----------
  servoSmooth = 0.75f * servoSmooth + 0.25f * targetRoll;
  servoPitch  = 0.75f * servoPitch  + 0.25f * targetPitch;

  servoSmooth = constrain(servoSmooth, 0, 180);
  servoPitch  = constrain(servoPitch,  0, 180);

  // ---------- NATIVE SERVO WRITE ----------
  setServoAngle(SERVO_PINR, (int)servoSmooth);
  setServoAngle(SERVO_PINP, (int)servoPitch);

  // ---------- LOOP TIMING PROFILER ----------
  unsigned long loopDuration = micros() - loopStartMicros;
  if (loopDuration < loopTimeMin) loopTimeMin = loopDuration;
  if (loopDuration > loopTimeMax) loopTimeMax = loopDuration;
  loopTimeSum += loopDuration;
  loopCount++;

  // ═══════════════════════════════════════
  // SCHEDULED DIAGNOSTICS & TELEMETRY
  // ═══════════════════════════════════════
  if (currentMillis - lastSatWarning > 500) {
      bool sat = false;
      if (output >= 90.0 || output <= -90.0)   { DEBUG_WARNING("Roll Saturated"); sat = true; }
      if (outputP >= 90.0 || outputP <= -90.0) { DEBUG_WARNING("Pitch Saturated"); sat = true; }
      if (sat) lastSatWarning = currentMillis;
  }

  if (currentMillis - lastHealthTimer >= 1000) {
      lastHealthTimer = currentMillis;
      Wire.beginTransmission(0x68);
      if (Wire.endTransmission() != 0) mpu.begin();
  }

  if (currentMillis - lastLoopStatsTimer >= 1000) {
      lastLoopStatsTimer = currentMillis;
      if (loopCount > 0) {
          float avgTime = (float)loopTimeSum / loopCount;
          Serial.println("\n[LOOP TIMING]");
          Serial.printf("  Average: %.2f us\n  Minimum: %lu us\n  Maximum: %lu us\n", avgTime, loopTimeMin, loopTimeMax);
      }
      loopTimeMin = 999999; loopTimeMax = 0; loopTimeSum = 0; loopCount = 0;
  }

  if (currentMillis - lastMemTimer >= 5000) {
      lastMemTimer = currentMillis;
      Serial.println("\n[MEMORY MONITOR]");
      Serial.printf("  Free Heap: %u Bytes\n", ESP.getFreeHeap());
  }

  if (currentMillis - lastTelemetryTimer >= 250) {
      lastTelemetryTimer = currentMillis;
      if (currentLogLevel >= LEVEL_INFO) {
          Serial.println("\n--- TELEMETRY ---");
          Serial.printf("Roll  | Angle: %5.2f | PID Output: %5.2f | Servo Target: %5.2f\n", angle, output, servoSmooth);
          Serial.printf("Pitch | Angle: %5.2f | PID Output: %5.2f | Servo Target: %5.2f\n", pitch, outputP, servoPitch);
      }
  }

  esp_task_wdt_reset();
  delay(10);
}

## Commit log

2026-04-20 Created GYRA print file 1
    [GYRO base handle axis 1 (yaw) v8 (ASSEMBLY).step, GYRO base handle axis 1 (yaw) v8 (PRINT V1).step]
2026-04-21 ROLL AND YAW AXES CAD FILES DEVELOPMENT
    roll and yaw axes 3d print cad files generation
    [GYRO base handle axis 1 (yaw) v8 (ASSEMBLY).step, GYRO base handle axis 1 (yaw) v8 (PRINT V1).step, GYRO part 1 base handle axis 1 (yaw) v10 (print 1).step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]
2026-04-22 updated CAD files and started development of code
    [GYRO part 2 base handle axis 1 (yaw) v10 (print 1).step, Gyra part 2 yaw and roll axis print v7 (print 2).step, Gyra part 2 yaw and roll axis print v7.step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]
2026-04-23 added more cad files
    [Gyra part 2 yaw and roll axis print v7.3mf]
2026-04-23 updated tolerance for yaw roll bracket
    [Gyra part 2 yaw and roll axis print v7.3mf, Gyra part 2 yaw and roll axis print v7.step]
2026-04-27 UPDATED CODE AND CAD FILES
    [GYRO part 1 base handle axis 1 (yaw) v10 (print 1).step]
2026-04-28 ADDED PID AND FINALIZED THE PROTOTYPE CODE
2026-04-29 updated code added PID tuning debugging methods
2026-05-01 Started work on GYRA prototype V2
    [GYRA PROTOTYPE V2 FULL ASSEMBLY v2.step, GYRA ROLL PITCH BRAKET PROTOTYPE V2 v5.step]
2026-05-01 added print filed bambu lab
    [GYRA ROLL PITCH BRAKET PROTOTYPE V2 v5.3mf]
2026-05-02 updated and added cad files
    improved yaw roll bracket cad file and developed roll pitch bracket and mpu6050 mount
    [GYRA PITCH BRACKET PROTOTYPE V1 v2.step, GYRA PROTOTYPE V2 FULL ASSEMBLY v2.step, GYRA ROLL PITCH BRAKET PROTOTYPE V2 v11.step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]
2026-05-05 updated code and 3d designs
    [GYRA PITCH BRACKET PROTOTYPE V1 v4.step, GYRA ROLL PITCH BRAKET PROTOTYPE V2 v13.step, GYRS MPU MOUNT FOR PROTOTYPE V2 v1.3mf]
2026-05-06 updates arduino code for GYRA
2026-05-08 updated code and cad but cad files not exported
2026-05-09 UPDATED CAD DESIGNS
2026-05-14 ADDED / UPDATED CAD FILES FOR GYRS
    [GYRA PITCH ARM V3 v17.step, GYRA PITCH BRACKET v18.step, GYRA ROLL PITCH BRAKET PROTOTYPE V2 v10.step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]
2026-05-15 updated tolerances
    [GYRA PITCH ARM V3 v18.step, GYRA PITCH ARMs updated.3mf, GYRA PITCH BRACKET v23.step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]
2026-05-17 ADDED AND UPDATED PRINT FILES
    [GYRA PITCH ARM V3 v20.step, GYRA PITCH BRACKET v27.step, GYRA ROLL PITCH BRAKET PROTOTYPE V2 v15.step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]
2026-05-24 mark1 begin
    created mark-1
    created base handle w/ bat holder
    orgainzed all files
    [GYRA BASE HANDEL PRINT 1.step, GYRA MARK-1 ASSEMBLY .step, GYRA PITCH ARM PRINT 2.step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]
2026-05-25 designed gyra_motherboard pcb schematics
    [GYRA_motherboard.kicad_pcb, GYRA_motherboard.kicad_sch]
2026-05-25 COMPLETED PCB
    COMPLETED GYRA_MARK-1_MOTHERBOARD
    [GYRA_motherboard-B_Cu.gbr, GYRA_motherboard-B_Mask.gbr, GYRA_motherboard-B_Paste.gbr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]
2026-05-26 finalized cad design for GYRA mark-1
2026-05-27 updated and organized and exported cad stuff
    [GYRA BASE HANDEL PRINT 1.step, GYRA BASE HANDLE.3mf, GYRA BASE HANDLE.step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]
2026-05-27 CREATED GYRA BOM FILE
    [BOM.csv]
2026-05-29 finalizing all files before submitting
    [BOM.csv, GYRA BASE HANDLE.3mf, GYRA BASE HANDLE.step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]
2026-06-01 updated cad enclosure for peekabot
    [GYRA BASE PCB ENCLOSURE v9.3mf, GYRA BASE PCB ENCLOSURE v9.f3d, GYRA BASE PCB ENCLOSURE v9.step]
